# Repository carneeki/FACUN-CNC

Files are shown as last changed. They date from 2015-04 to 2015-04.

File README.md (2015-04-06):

# FACUN-CNC
It's not FANUC. It's FUCAN!

FUCAN CNC is a collection of circuits designed to enable connection of an
Arduino, probably running Grbl, to the "real world", that is, your stepper
controllers, limit switches, push buttons and pendants (if applicable), and so
on.

Developed by an impoverished university student, it is designed to be budget
conscious, whilst minimising compromises on things that are nice to have. One
example is that all logic components are in DIP form factor so they can be
socketed and easily replaced in the event that the magic smoke escapes a
component.

## TRI-LIMIT-INTERFACE
TRI-LIMIT-INTERFACE is a 3 axis limit switch debounce and logical OR board.
Because we often have limit switches at each end of our axis limits, this
handles debouncing both ends, and sending a single clean signal to the Arduino.

Grbl has some debounce routines in it, but having this board enables changing to
other systems that may not have debouncing built in.

## LIMIT-INTERFACE
LIMIT-INTERFACE is a single axis, strip board version of the 3 axis board. Not
everyone can fab a PCB, and not everyone can afford to have the large 3 axis
board professionally fabbed. The strip board version can be easily made (and
tripled) while getting started. Once you are up and running, you should be able
to route the TRI version if you are so inclined.

## PUSHBUTTON-DEBOUNCE
PUSHBUTTON-DEBOUNCE is a board for debouncing pushbutton switches.

## ArduinoMiniPro Breakout
The Arduino Mini Pro is a really neat little board. It takes an Arduino and puts
it into a wide DIP array.

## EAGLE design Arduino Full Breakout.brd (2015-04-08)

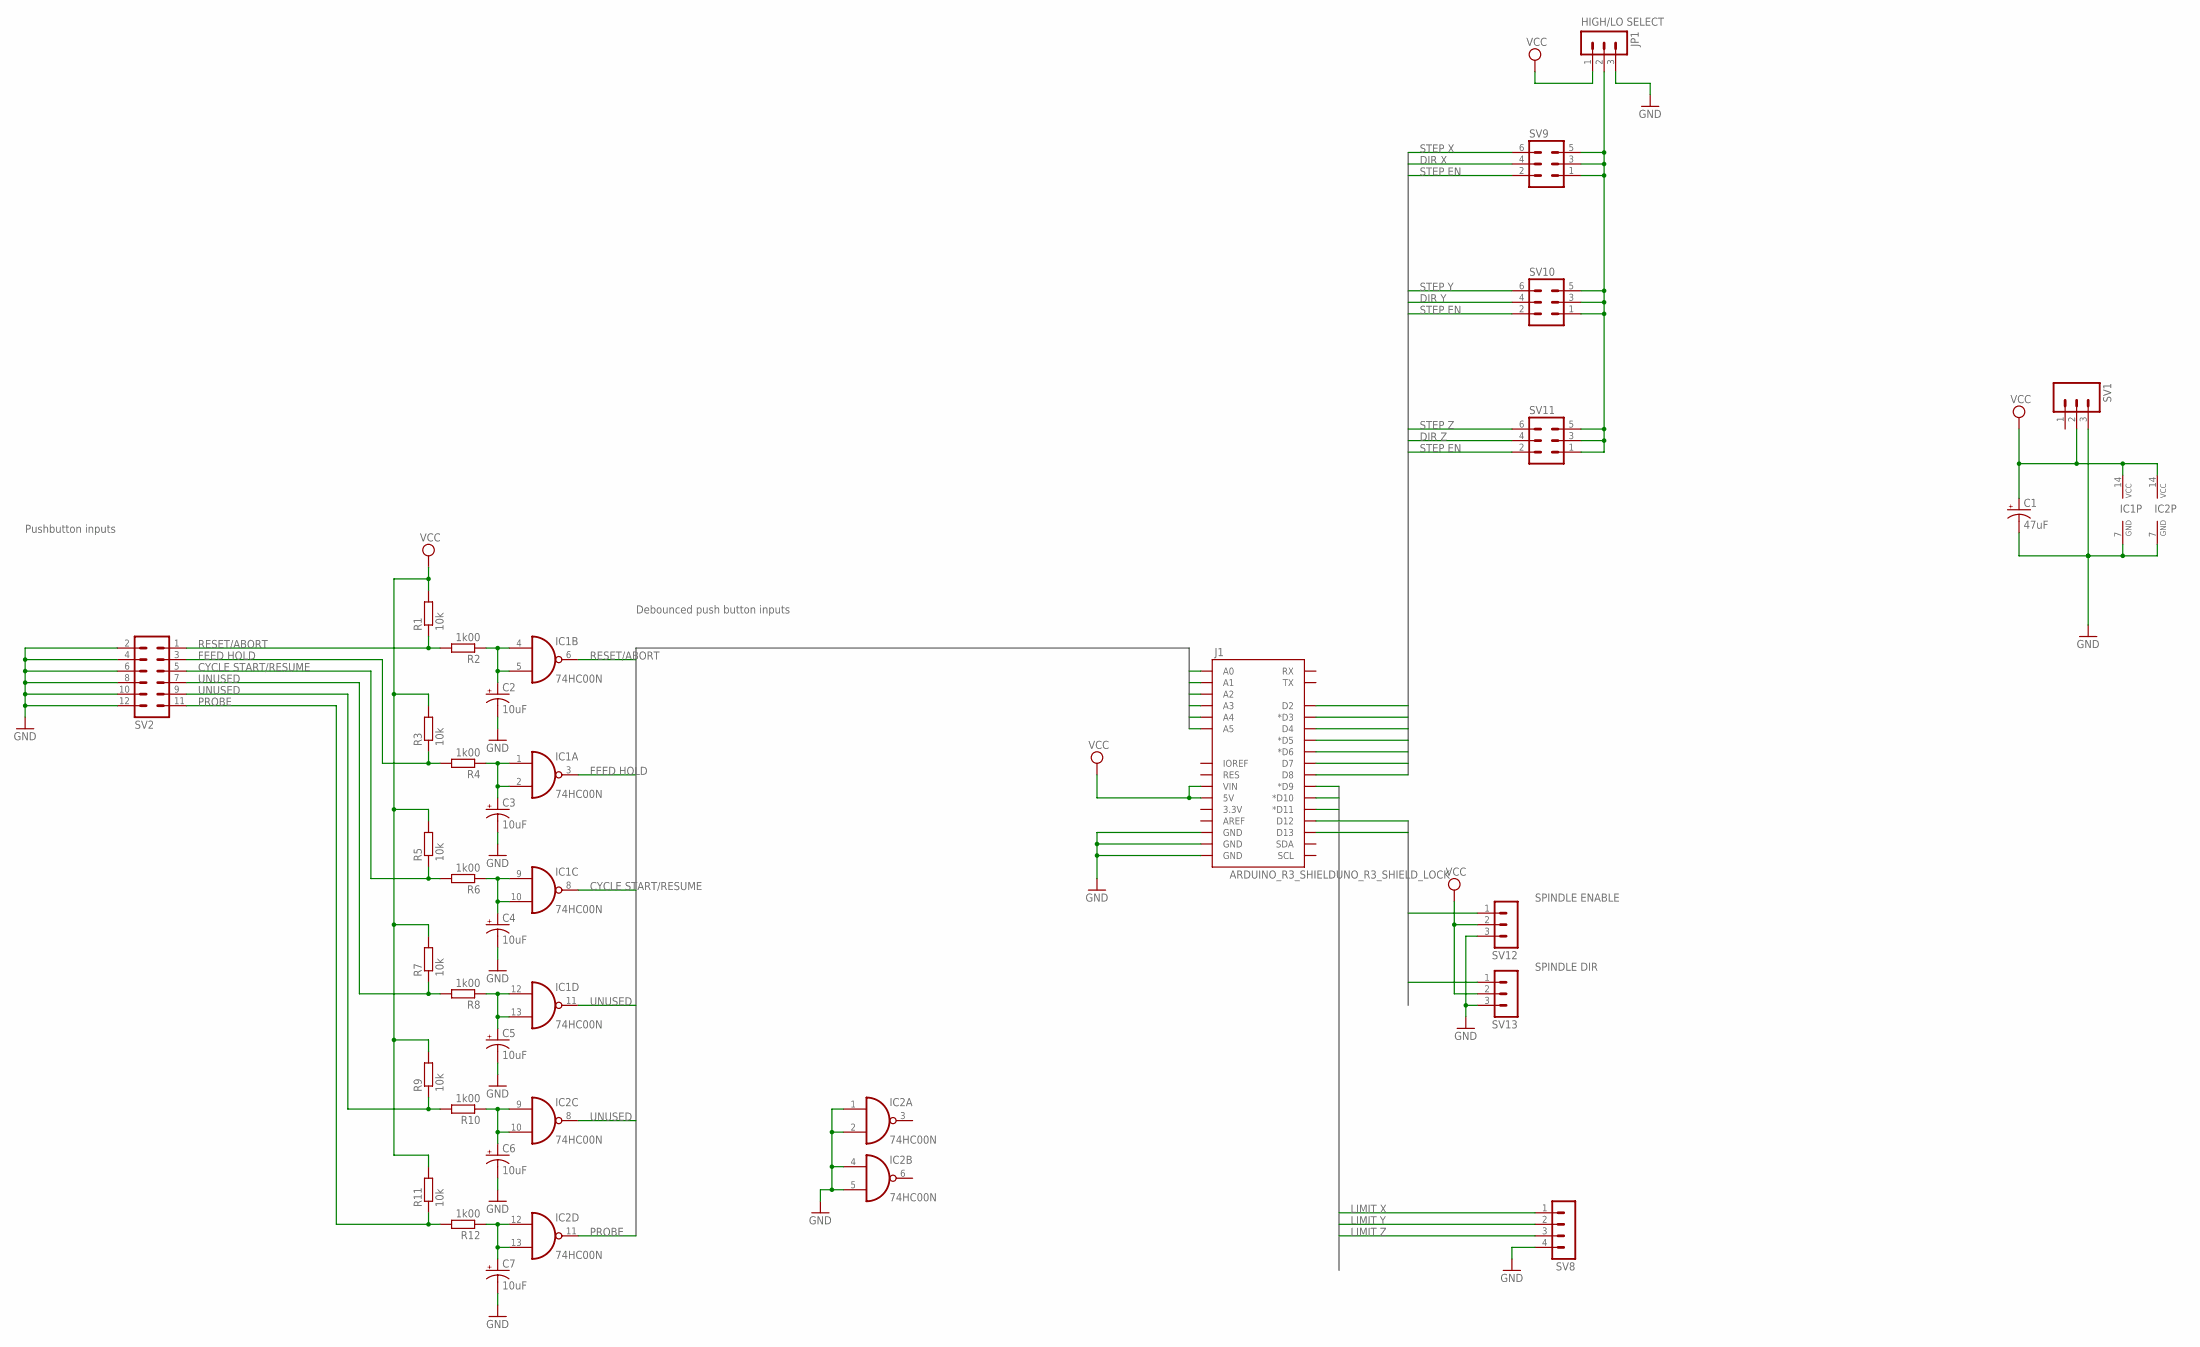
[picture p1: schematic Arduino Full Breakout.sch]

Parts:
C1: 47uF; CPOL-RADIAL-10UF-25V
C2, C3, C4, C5, C6, C7: 10uF; CPOL-RADIAL-10UF-25V
IC1, IC2: 74HC00N; DIL14
J1: ARDUINO_R3_SHIELDUNO_R3_SHIELD_LOCK; UNO_R3_SHIELD_LOCK
JP1: MA03-1
R1, R11: 10k; 0207/5V
R2, R4, R6, R8, R10, R12: 1k00; 0207/7
R3, R9: 10k; 0207/7
R5, R7: 10k; 0207/10
SV1: M03-SCREW-5MM; SCREWTERMINAL-5MM-3
SV2: MA06-2
SV8: MA04-1
SV9, SV10, SV11: MA03-2
SV12, SV13: MA03-1

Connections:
BUTTONS0: IC1.6 (O), J1.A0
BUTTONS1: IC1.3 (O), J1.A1
BUTTONS2: IC1.8 (O), J1.A2
BUTTONS3: IC1.11 (O), J1.A3
BUTTONS4: IC2.8 (O), J1.A4
BUTTONS5: IC2.11 (O), J1.A5
GND: C1.2 (-), C2.2 (-), C3.2 (-), C4.2 (-), C5.2 (-), C6.2 (-), C7.2 (-), IC1.7 (GND), IC2.1 (I0), IC2.2 (I1), IC2.4 (I0), IC2.5 (I1), IC2.7 (GND), J1.GND@0 (GND), J1.GND@1 (GND), J1.GND@2 (GND), JP1.3, SV1.3, SV2.2, SV2.4, SV2.6, SV2.8, SV2.10, SV2.12, SV8.4, SV12.3, SV13.3
LIMITS0: J1.D9 (*D9), SV8.1
LIMITS1: J1.D10 (*D10), SV8.2
LIMITS2: J1.D11 (*D11), SV8.3
unnamed: JP1.2, SV9.1, SV9.3, SV9.5, SV10.1, SV10.3, SV10.5, SV11.1, SV11.3, SV11.5
unnamed: C2.1 (+), IC1.4 (I0), IC1.5 (I1), R2.1
unnamed: R1.1, R2.2, SV2.1
unnamed: C3.1 (+), IC1.1 (I0), IC1.2 (I1), R4.1
unnamed: R3.1, R4.2, SV2.3
unnamed: C4.1 (+), IC1.9 (I0), IC1.10 (I1), R6.1
unnamed: R5.1, R6.2, SV2.5
unnamed: C5.1 (+), IC1.12 (I0), IC1.13 (I1), R8.1
unnamed: R7.1, R8.2, SV2.7
unnamed: C6.1 (+), IC2.9 (I0), IC2.10 (I1), R10.1
unnamed: R9.1, R10.2, SV2.9
unnamed: C7.1 (+), IC2.12 (I0), IC2.13 (I1), R12.1
unnamed: R11.1, R12.2, SV2.11
SPINDLE0: J1.D12, SV12.1
SPINDLE1: J1.D13, SV13.1
STEP0: J1.D2, SV9.6
STEP1: J1.D3 (*D3), SV10.6
STEP2: J1.D4, SV11.6
STEP3: J1.D5 (*D5), SV9.4
STEP4: J1.D6 (*D6), SV10.4
STEP5: J1.D7, SV11.4
STEP6: J1.D8, SV9.2, SV10.2, SV11.2
VCC: C1.1 (+), IC1.14 (VCC), IC2.14 (VCC), J1.VIN, JP1.1, R1.2, R3.2, R5.2, R7.2, R9.2, R11.2, SV1.2, SV12.2, SV13.2

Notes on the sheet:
RESET/ABORT
FEED HOLD
CYCLE START/RESUME
UNUSED
PROBE
SPINDLE DIR
SPINDLE ENABLE
LIMIT X
LIMIT Y
LIMIT Z
STEP X
STEP Y
HIGH/LO SELECT
DIR X
DIR Y
STEP Z
DIR Z
STEP EN
Debounced push button inputs
Pushbutton inputs

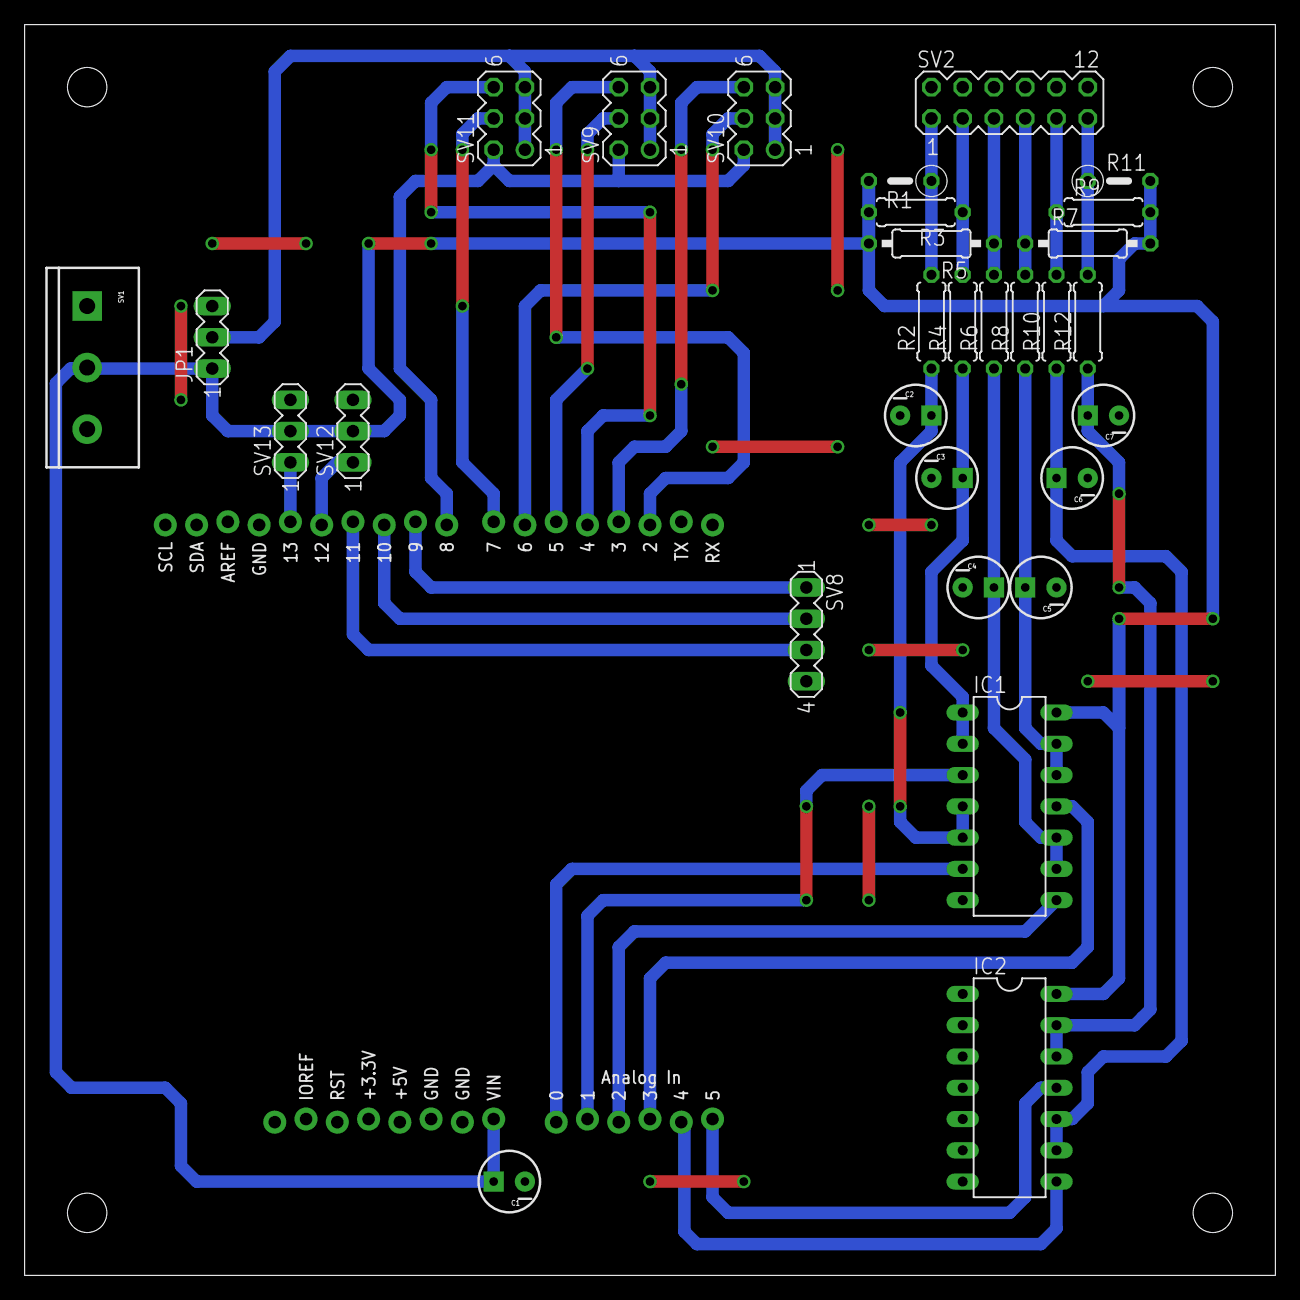
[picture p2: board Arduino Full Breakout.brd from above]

Board: 2 copper layers, 101.6 x 101.6 mm, 31 parts (0 on the bottom side), 33 nets.

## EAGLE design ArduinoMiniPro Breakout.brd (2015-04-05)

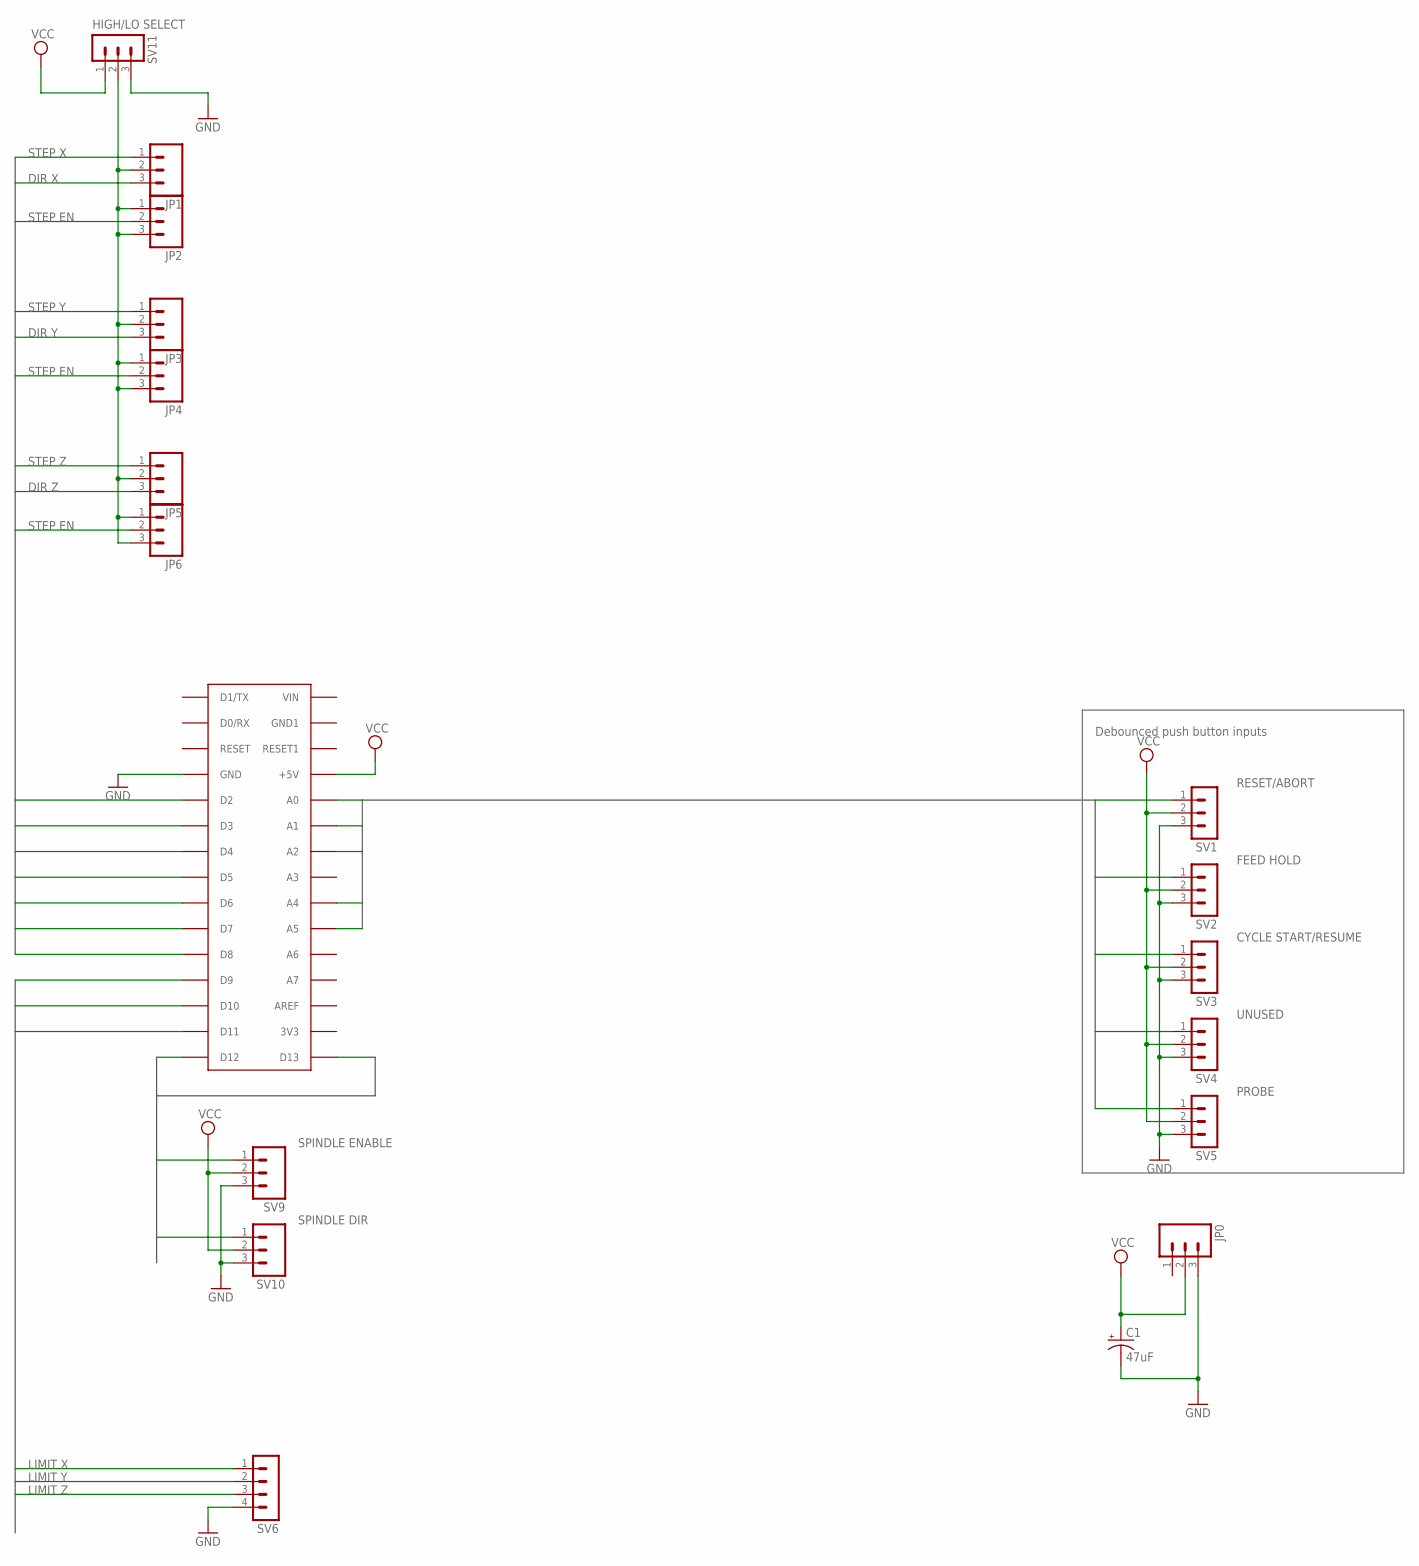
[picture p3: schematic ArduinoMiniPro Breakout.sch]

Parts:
C1: 47uF; CPOL-RADIAL-10UF-25V
JP0, JP1, JP2, JP3, JP4, JP5, JP6: M03-SCREW-5MM; SCREWTERMINAL-5MM-3
SV1, SV2, SV3, SV4, SV5, SV11: MA03-1
SV6: MA04-1
SV9, SV10: M03-SCREW-5MM; SCREWTERMINAL-5MM-3
U$2: ARDUINONANO; PDIP-32

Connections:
B0: SV1.1, U$2.A0
B1: SV2.1, U$2.A1
B2: SV3.1, U$2.A2
B4: SV4.1, U$2.A4
B5: SV5.1, U$2.A5
GND: C1.2 (-), JP0.3, SV1.3, SV2.3, SV3.3, SV4.3, SV5.3, SV6.4, SV9.3, SV10.3, SV11.3, U$2.GND
LIMITS0: SV6.1, U$2.D9
LIMITS1: SV6.2, U$2.D10
LIMITS2: SV6.3, U$2.D11
unnamed: JP1.2, JP2.1, JP2.3, JP3.2, JP4.1, JP4.3, JP5.2, JP6.1, JP6.3, SV11.2
SPINDLE0: SV9.1, U$2.D12
SPINDLE1: SV10.1, U$2.D13
STEP0: JP1.1, U$2.D2
STEP1: JP3.1, U$2.D3
STEP2: JP5.1, U$2.D4
STEP3: JP1.3, U$2.D5
STEP4: JP3.3, U$2.D6
STEP5: JP5.3, U$2.D7
STEP6: JP2.2, JP4.2, JP6.2, U$2.D8
VCC: C1.1 (+), JP0.2, SV1.2, SV2.2, SV3.2, SV4.2, SV5.2, SV9.2, SV10.2, SV11.1, U$2.+5V

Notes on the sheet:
RESET/ABORT
FEED HOLD
CYCLE START/RESUME
UNUSED
PROBE
SPINDLE DIR
SPINDLE ENABLE
LIMIT X
LIMIT Y
LIMIT Z
STEP X
STEP Y
HIGH/LO SELECT
DIR X
DIR Y
STEP Z
DIR Z
STEP EN
Debounced push button inputs

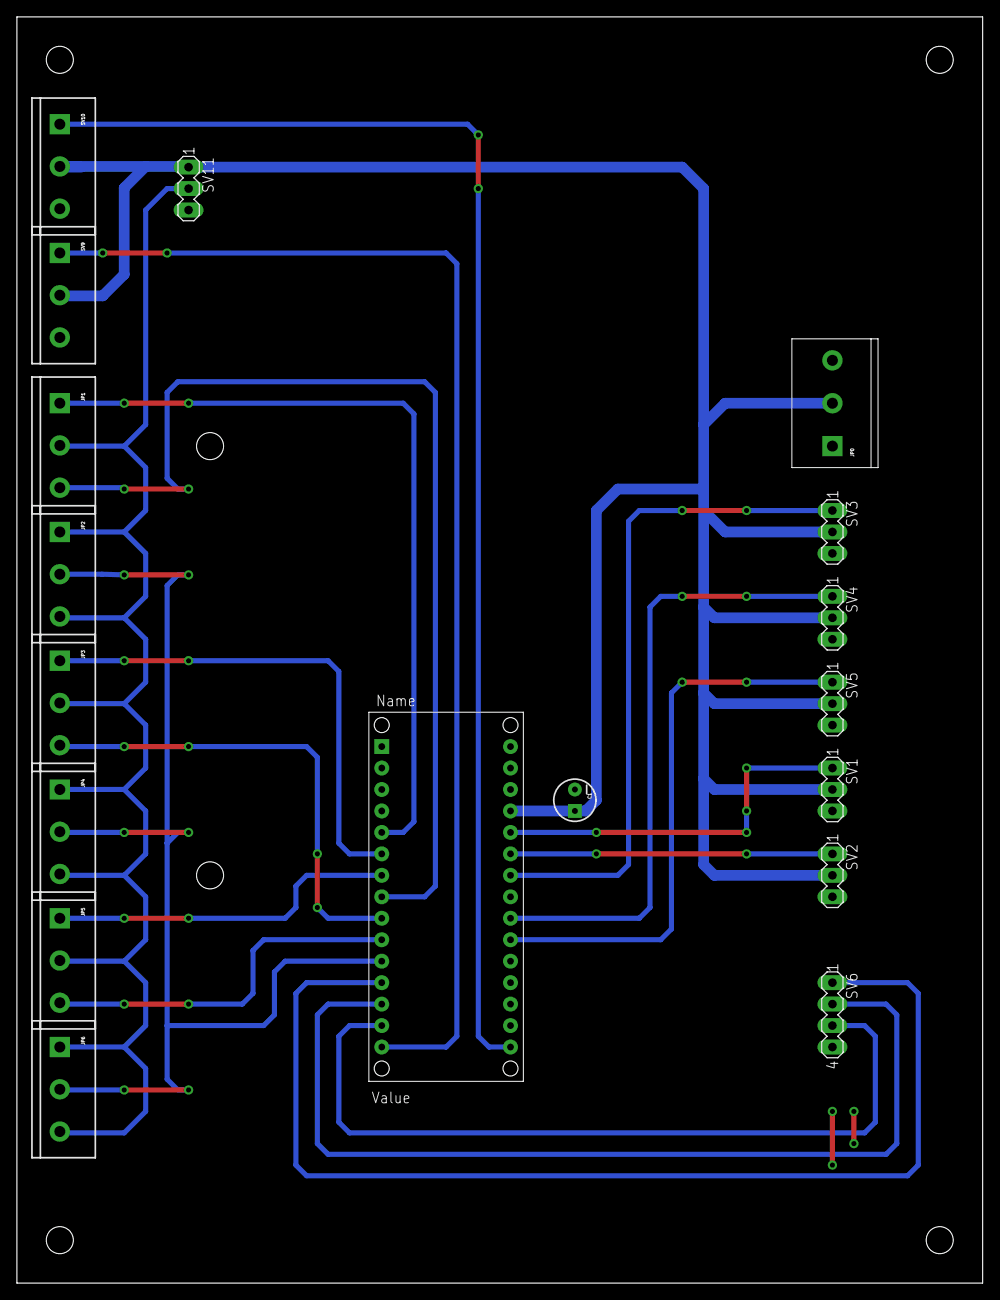
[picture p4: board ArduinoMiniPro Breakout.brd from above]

Board: 2 copper layers, 114.3 x 149.9 mm, 18 parts (0 on the bottom side), 20 nets.

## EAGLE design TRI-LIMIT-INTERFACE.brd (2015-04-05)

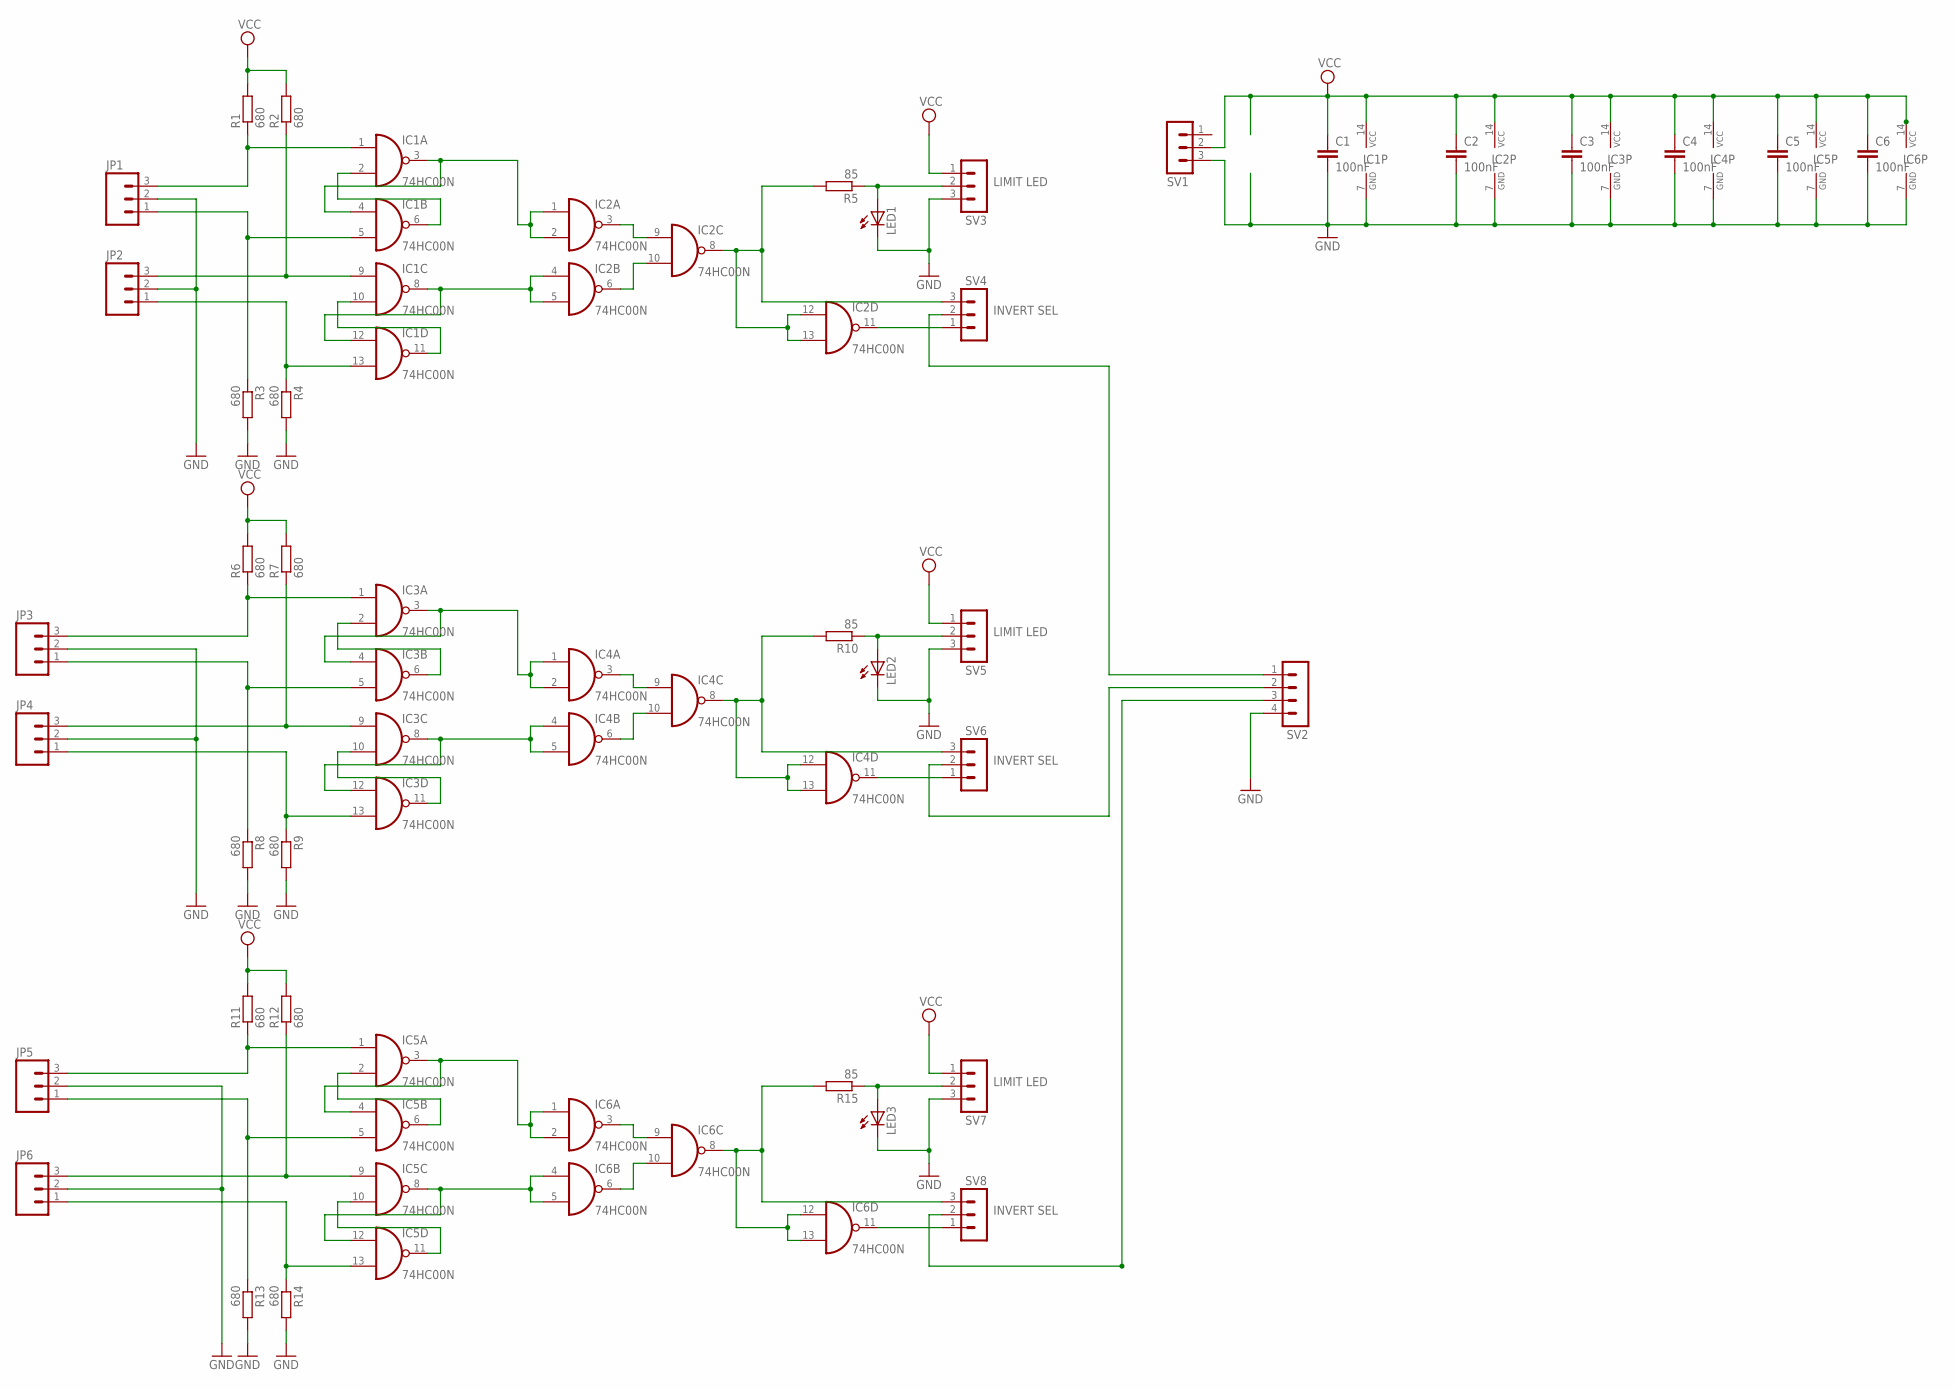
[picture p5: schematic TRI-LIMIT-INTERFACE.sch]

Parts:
C1, C2, C3, C4, C5, C6: 100nF; CAP-PTH-SMALL
IC1, IC2, IC3, IC4, IC5, IC6: 74HC00N; DIL14
JP1, JP2, JP3, JP4, JP5, JP6: M03-SCREW-5MM; SCREWTERMINAL-5MM-3
LED1, LED2, LED3: LED3MM
R1, R2, R3, R4, R6, R7, R8, R9, R11, R12, R13, R14: 680; 0207/7
R5, R10, R15: 85; 0207/10
SV1, SV3, SV4, SV5, SV6, SV7, SV8: MA03-1
SV2: MA04-1

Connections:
/SIG: IC2.11 (O), SV4.1
/SIG1: IC4.11 (O), SV6.1
/SIG2: IC6.11 (O), SV8.1
GND: C1.2, C2.2, C3.2, C4.2, C5.2, C6.2, IC1.7 (GND), IC2.7 (GND), IC3.7 (GND), IC4.7 (GND), IC5.7 (GND), IC6.7 (GND), JP1.2, JP2.2, JP3.2, JP4.2, JP5.2, JP6.2, LED1.K (C), LED2.K (C), LED3.K (C), R3.2, R4.2, R8.2, R9.2, R13.2, R14.2, SV1.3, SV2.4, SV3.3, SV5.3, SV7.3
unnamed: IC1.3 (O), IC1.4 (I0), IC2.1 (I0), IC2.2 (I1)
unnamed: IC1.2 (I1), IC1.6 (O)
unnamed: IC1.13 (I1), JP2.1, R4.1
unnamed: IC1.5 (I1), JP1.1, R3.1
unnamed: IC1.8 (O), IC1.12 (I0), IC2.4 (I0), IC2.5 (I1)
unnamed: IC1.10 (I1), IC1.11 (O)
unnamed: IC1.9 (I0), JP2.3, R2.1
unnamed: IC1.1 (I0), JP1.3, R1.1
unnamed: IC2.3 (O), IC2.9 (I0)
unnamed: IC2.6 (O), IC2.10 (I1)
unnamed: IC3.3 (O), IC3.4 (I0), IC4.1 (I0), IC4.2 (I1)
unnamed: IC3.2 (I1), IC3.6 (O)
unnamed: IC3.1 (I0), JP3.3, R6.1
unnamed: IC3.5 (I1), JP3.1, R8.1
unnamed: IC3.8 (O), IC3.12 (I0), IC4.4 (I0), IC4.5 (I1)
unnamed: LED1.A, R5.1, SV3.2
unnamed: IC3.10 (I1), IC3.11 (O)
unnamed: IC3.9 (I0), JP4.3, R7.1
unnamed: IC3.13 (I1), JP4.1, R9.1
unnamed: IC4.3 (O), IC4.9 (I0)
unnamed: IC4.6 (O), IC4.10 (I1)
unnamed: LED2.A, R10.1, SV5.2
unnamed: IC5.3 (O), IC5.4 (I0), IC6.1 (I0), IC6.2 (I1)
unnamed: IC5.2 (I1), IC5.6 (O)
unnamed: IC5.1 (I0), JP5.3, R11.1
unnamed: IC5.5 (I1), JP5.1, R13.1
unnamed: IC5.8 (O), IC5.12 (I0), IC6.4 (I0), IC6.5 (I1)
unnamed: IC5.10 (I1), IC5.11 (O)
unnamed: IC5.9 (I0), JP6.3, R12.1
unnamed: IC5.13 (I1), JP6.1, R14.1
unnamed: IC6.3 (O), IC6.9 (I0)
unnamed: IC6.6 (O), IC6.10 (I1)
unnamed: LED3.A, R15.1, SV7.2
SIG: IC2.8 (O), IC2.12 (I0), IC2.13 (I1), R5.2, SV4.3
SIG1: IC4.8 (O), IC4.12 (I0), IC4.13 (I1), R10.2, SV6.3
SIG2: IC6.8 (O), IC6.12 (I0), IC6.13 (I1), R15.2, SV8.3
TO_CPU0: SV2.1, SV4.2
TO_CPU1: SV2.2, SV6.2
TO_CPU2: SV2.3, SV8.2
VCC: C1.1, C2.1, C3.1, C4.1, C5.1, C6.1, IC1.14 (VCC), IC2.14 (VCC), IC3.14 (VCC), IC4.14 (VCC), IC5.14 (VCC), IC6.14 (VCC), R1.2, R2.2, R6.2, R7.2, R11.2, R12.2, SV1.2, SV3.1, SV5.1, SV7.1

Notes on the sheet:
INVERT SEL
LIMIT LED

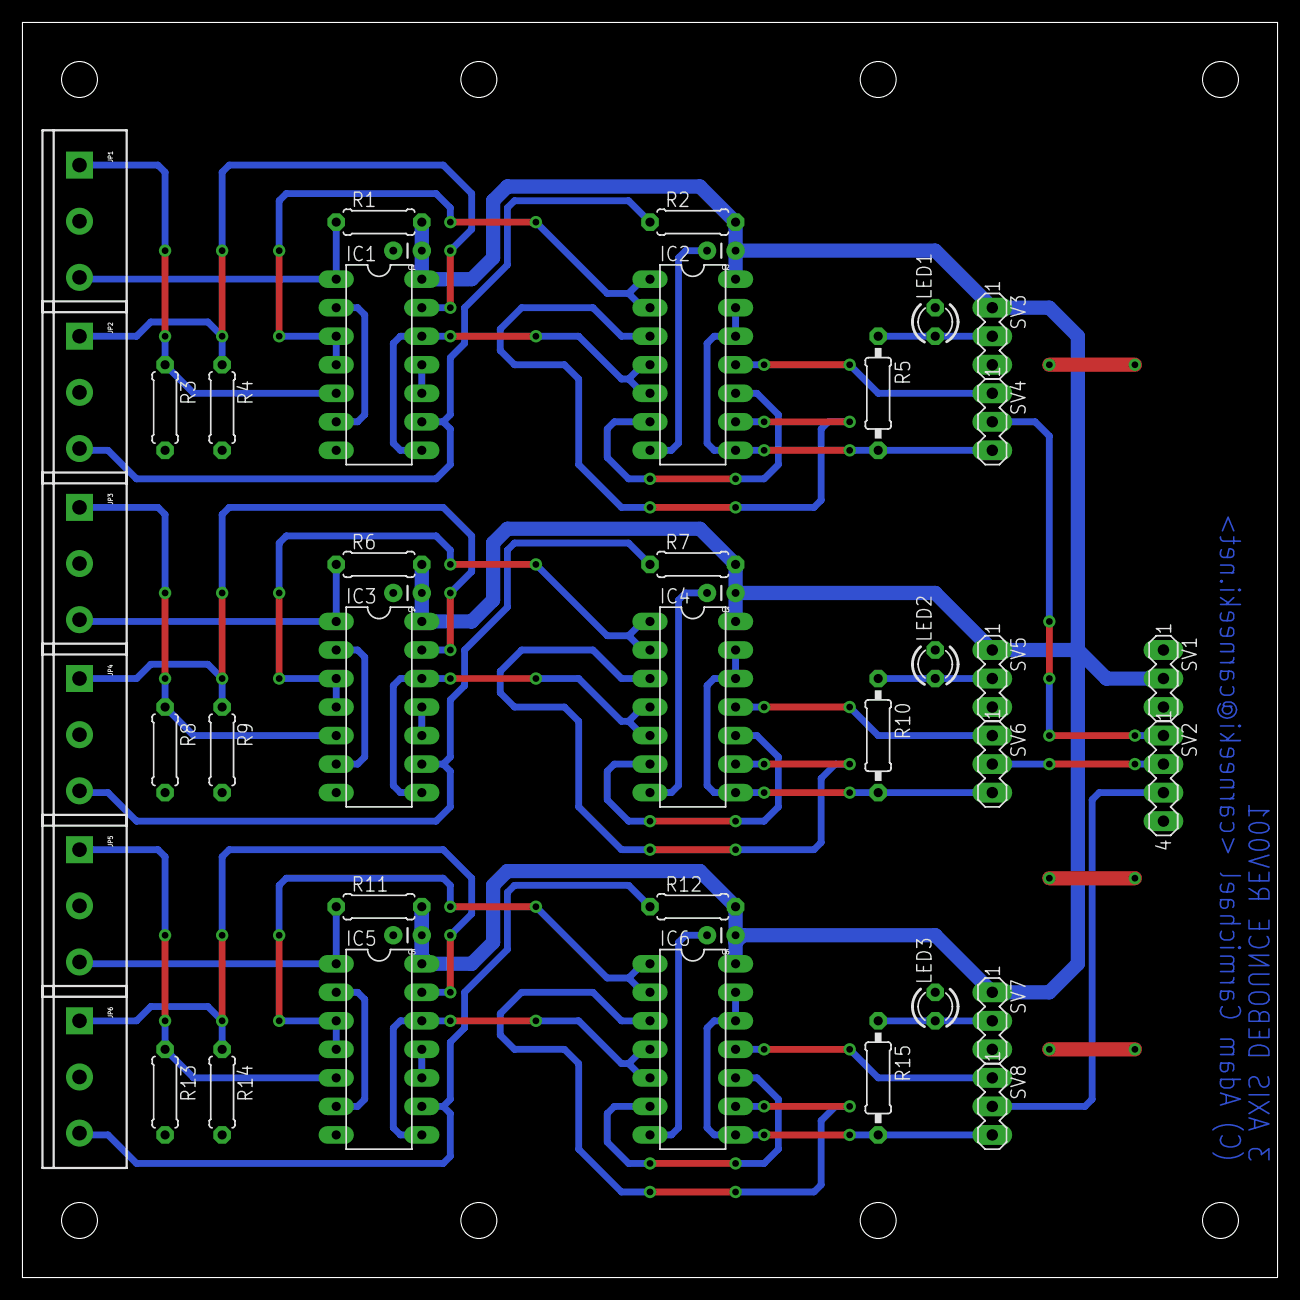
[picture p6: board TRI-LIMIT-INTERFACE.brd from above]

Board: 2 copper layers, 111.8 x 111.8 mm, 44 parts (0 on the bottom side), 44 nets.

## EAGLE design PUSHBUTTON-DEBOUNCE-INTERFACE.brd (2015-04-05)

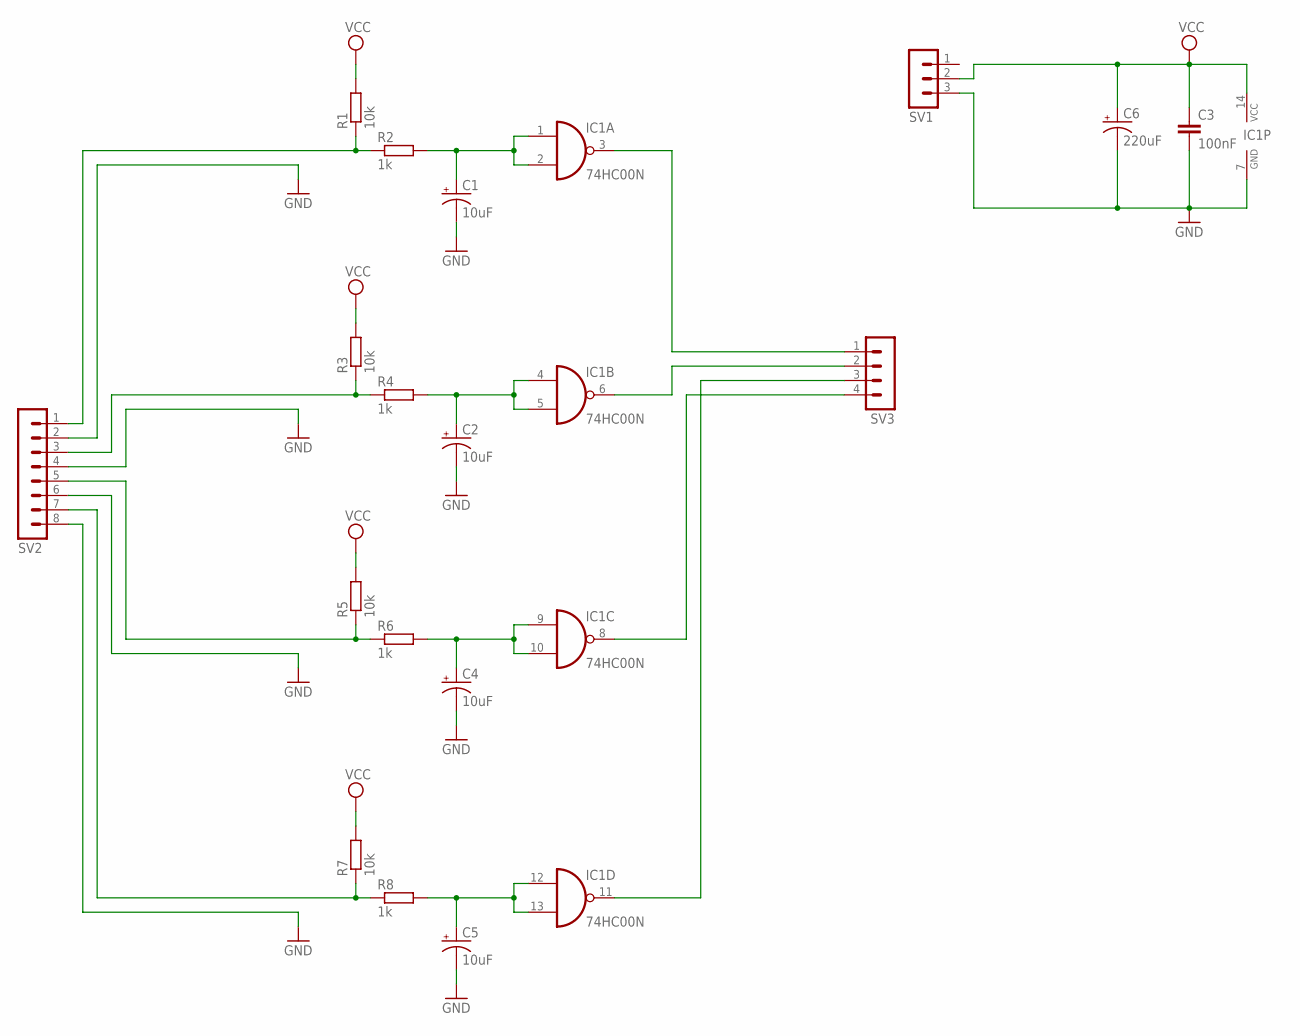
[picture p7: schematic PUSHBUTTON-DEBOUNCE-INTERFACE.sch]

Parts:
C1, C2, C4, C5: 10uF; CPOL-RADIAL-100UF-25V
C3: 100nF; CAP-PTH-SMALL
C6: 220uF; CPOL-RADIAL-1000UF-25V
IC1: 74HC00N; DIL14
R1, R7: 10k; 0207/7
R2, R4, R6, R8: 1k; 0207/7
R3, R5: 10k; 0207/12
SV1: MA03-1
SV2: MA08-1
SV3: MA04-1

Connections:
GND: C1.2 (-), C2.2 (-), C3.2, C4.2 (-), C5.2 (-), C6.2 (-), IC1.7 (GND), SV1.3, SV2.2, SV2.4, SV2.6, SV2.8
unnamed: C1.1 (+), IC1.1 (I0), IC1.2 (I1), R2.2
unnamed: C2.1 (+), IC1.4 (I0), IC1.5 (I1), R4.2
unnamed: C4.1 (+), IC1.9 (I0), IC1.10 (I1), R6.2
unnamed: C5.1 (+), IC1.12 (I0), IC1.13 (I1), R8.2
unnamed: IC1.3 (O), SV3.1
unnamed: IC1.6 (O), SV3.2
unnamed: IC1.8 (O), SV3.4
unnamed: IC1.11 (O), SV3.3
unnamed: R1.1, R2.1, SV2.1
unnamed: R3.1, R4.1, SV2.3
unnamed: R5.1, R6.1, SV2.5
unnamed: R7.1, R8.1, SV2.7
VCC: C3.1, C6.1 (+), IC1.14 (VCC), R1.2, R3.2, R5.2, R7.2, SV1.2

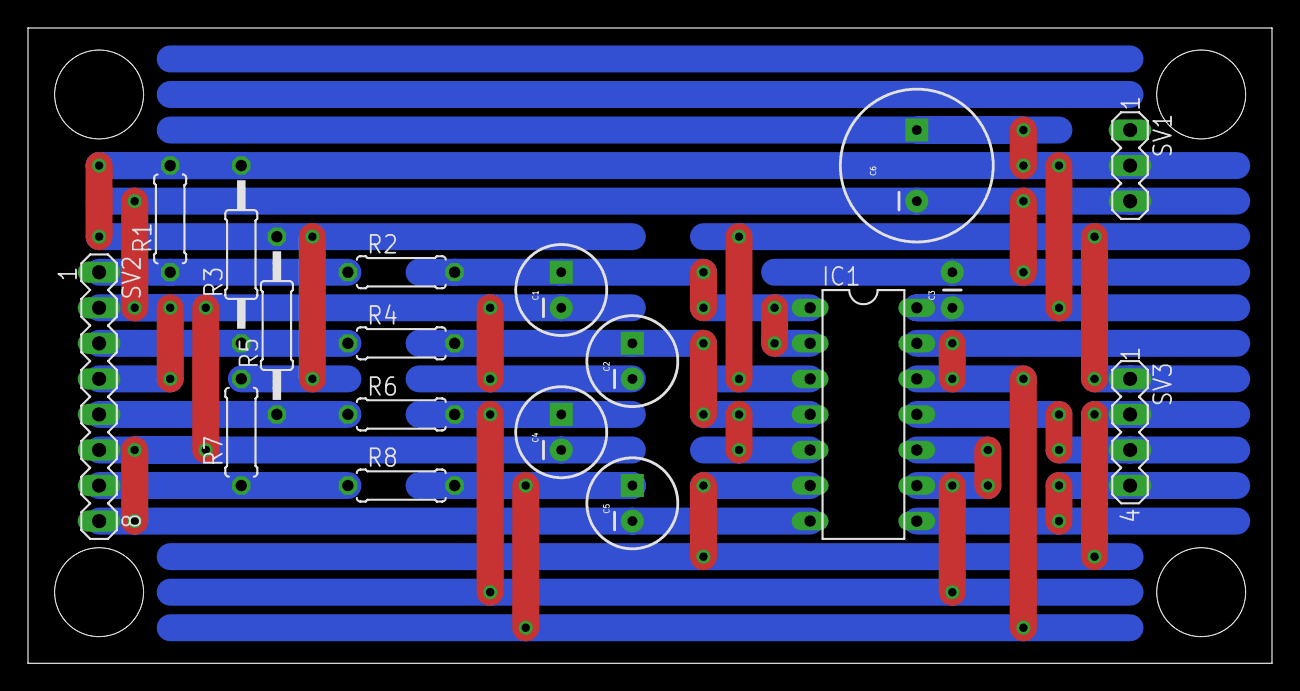
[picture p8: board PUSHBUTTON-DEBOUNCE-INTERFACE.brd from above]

Board: 2 copper layers, 88.9 x 45.4 mm, 18 parts (0 on the bottom side), 14 nets.

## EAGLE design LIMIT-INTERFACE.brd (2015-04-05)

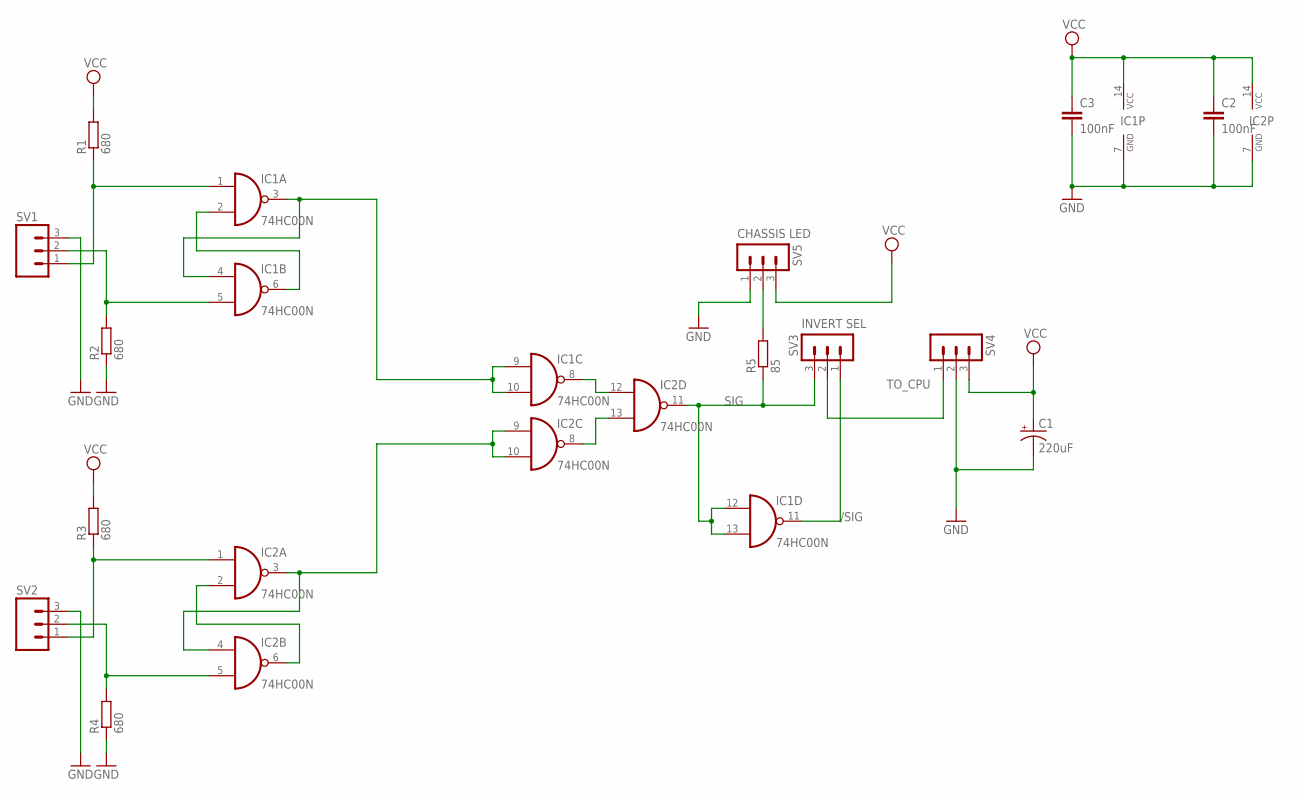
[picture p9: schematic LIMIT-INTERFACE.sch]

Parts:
C1: 220uF; CPOL-RADIAL-1000UF-25V
C2, C3: 100nF; CAP-PTH-SMALL
IC1, IC2: 74HC00N; DIL14
R1, R3: 680; 0207/7
R2, R4: 680; 0207/5V
R5: 85; 0207/10
SV1, SV2: M03-SCREW-5MM; SCREWTERMINAL-5MM-3
SV3, SV4, SV5: MA03-1

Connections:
/SIG: IC1.11 (O), SV3.1
GND: C1.2 (-), C2.2, C3.2, IC1.7 (GND), IC2.7 (GND), R2.1, R4.1, SV1.3, SV2.3, SV4.2, SV5.1
unnamed: IC1.3 (O), IC1.4 (I0), IC1.9 (I0), IC1.10 (I1)
unnamed: IC1.2 (I1), IC1.6 (O)
unnamed: IC1.1 (I0), R1.1, SV1.1
unnamed: IC1.5 (I1), R2.2, SV1.2
unnamed: IC2.3 (O), IC2.4 (I0), IC2.9 (I0), IC2.10 (I1)
unnamed: IC2.2 (I1), IC2.6 (O)
unnamed: IC2.1 (I0), R3.1, SV2.1
unnamed: IC2.5 (I1), R4.2, SV2.2
unnamed: IC1.8 (O), IC2.12 (I0)
unnamed: IC2.8 (O), IC2.13 (I1)
unnamed: R5.2, SV5.2
SIG: IC1.12 (I0), IC1.13 (I1), IC2.11 (O), R5.1, SV3.3
TO_CPU: SV3.2, SV4.1
VCC: C1.1 (+), C2.1, C3.1, IC1.14 (VCC), IC2.14 (VCC), R1.2, R3.2, SV4.3, SV5.3

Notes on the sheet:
INVERT SEL
CHASSIS LED

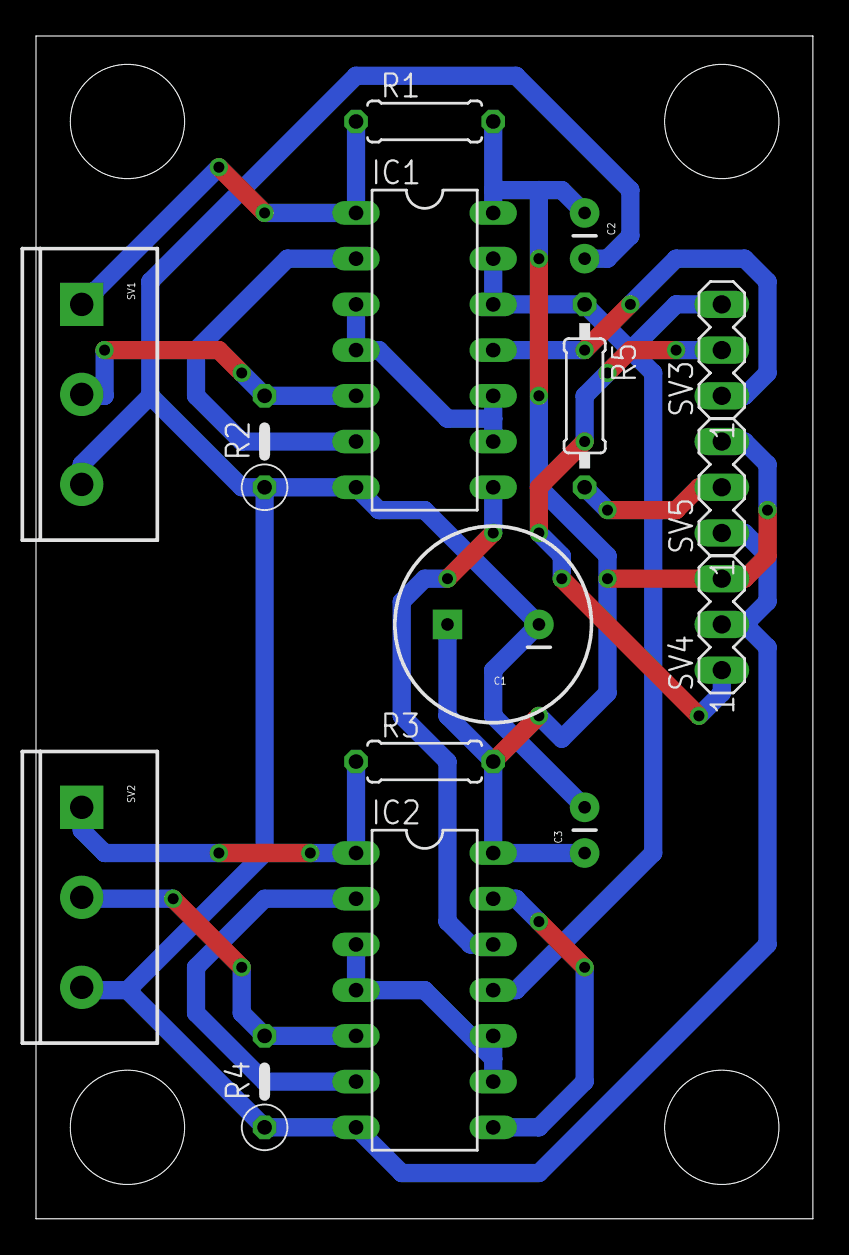
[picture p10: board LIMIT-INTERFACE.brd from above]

Board: 2 copper layers, 43.2 x 65.7 mm, 15 parts (0 on the bottom side), 16 nets.

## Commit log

2015-04-05 commit the first bunch of files
    [ArduinoMiniPro Breakout.brd, ArduinoMiniPro Breakout.sch, LIMIT-INTERFACE.brd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]
2015-04-05 Made the board a pure breakout board
    Rather than smooshing all the functions onto a single board, this board
    is purely for breaking out the pins to headers.
    Given the relatively large size, there is no reason a full size Arduino
    cannot be used, and so a full size breakout is on the way.
    [ArduinoMiniPro Breakout.brd, ArduinoMiniPro Breakout.sch]
2015-04-05 Full size breakout board
    I'm not 100% happy with how this turned out. TODO: come up with a
    consistent board between both mini and full size Arduinos.
    [Arduino Full Breakout.brd, Arduino Full Breakout.sch]
2015-04-08 add pushbutton debounce to full size breakout board
    [Arduino Full Breakout.brd, Arduino Full Breakout.sch]

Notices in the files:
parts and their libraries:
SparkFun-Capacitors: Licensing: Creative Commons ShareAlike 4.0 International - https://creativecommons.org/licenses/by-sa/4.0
